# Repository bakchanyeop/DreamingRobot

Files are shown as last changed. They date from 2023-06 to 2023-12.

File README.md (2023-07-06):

# DreamingRobot

본 저작권은 꿈꾸는 로봇에 있습니다!

<br>
https://www.youtube.com/@Dreamingrobot<br>
▲ 꿈꾸는 로봇 Youtube 주소

안녕하세요! 꿈꾸는 로봇 꿈봇입니다.

본 깃허브는 제가 제작하는 과정의 코드와 STL 파일들을 올릴 예정입니다.

5개월간 짬짬이 만들은 로봇입니다.

현재 4족 로봇을 로보티즈 다이나믹셀 AX12로 제작중입니다.

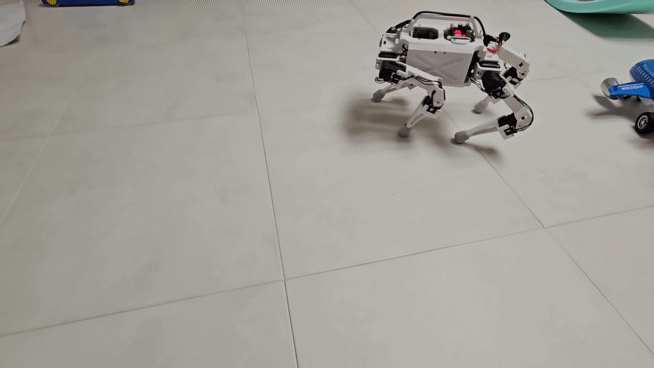
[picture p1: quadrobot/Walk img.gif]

▲ 보행 영상(이전 영상이라 지금 모델하고는 조금 차이가 있습니다)

# Model File

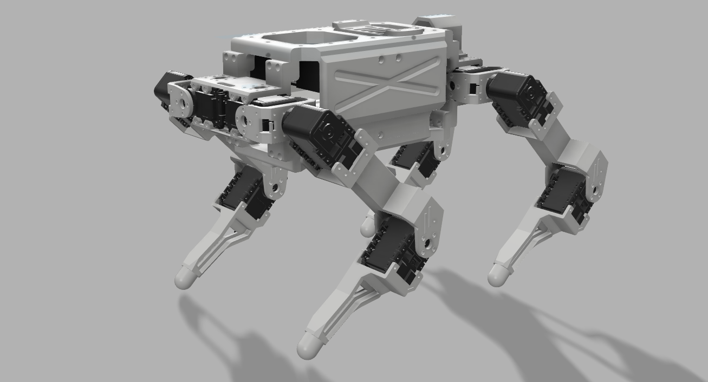
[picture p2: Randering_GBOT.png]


▲ 최종 조립 랜더링 이미지

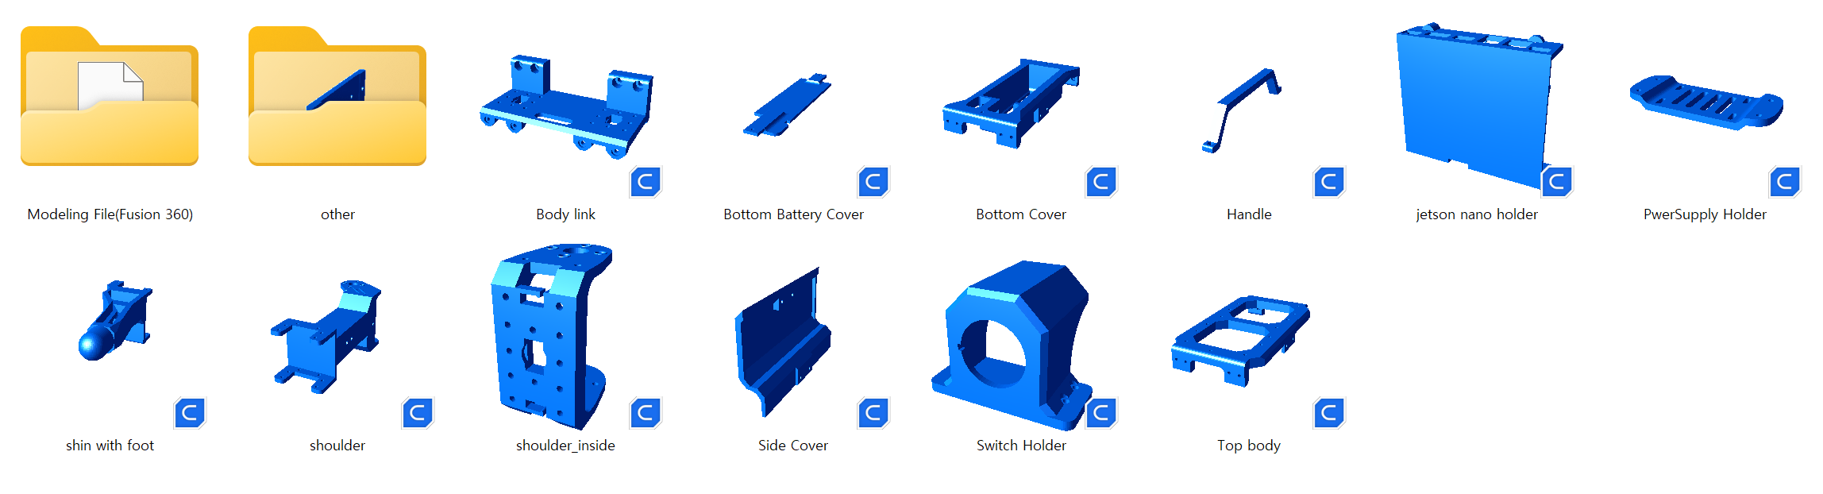
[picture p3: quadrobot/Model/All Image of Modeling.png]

' 모델 파일은 상단 이미지와 같으며 수량은 아래와 같습니다.

**Shoulder, Shin with foot은 큐라의 Mirror 기능으로 반대편 발도 출력 합니다.**

|순번|제목|수량|
|---|---|---|
|1|Body link|4EA|
|2|Bottom Battery Cover|1EA|
|3|Bottom Cover|1EA|
|4|Handle|1EA|
|5|jetson nano(ver.2GB Dev) holder|1EA|
|6|shoulder(right)|2EA|
|7|shoulder(left)|2EA|
|8|Shin with foot(right)|2EA|
|9|Shin with foot(left)|2EA|
|10|Sude Civer|2EA|
|11|Switch Holder|1EA|
|12|Top Body|1EA|
|13|shoulder_inside|1EA|

# 부속품

|순번|제목|수량|
|---|---|---|
|1|M2x8 Bolt Nut Set|52 EA|
|2|M2x6|48EA|
|3|M3x10 Bolt nut set|8Set|
|4|M3x10 Bolt|22EA|
|5|U2D2 변환기|1EA|
|6|젯슨나노2GB버전|1EA|
|7|XH-M609(리튬폴리머 방전 방지)|1EA|
|8|Switch|1EA|
|9|lithium Polymer 30C(11.1V)|1EA|
|10|Joystick|1EA|

# 조립 내용

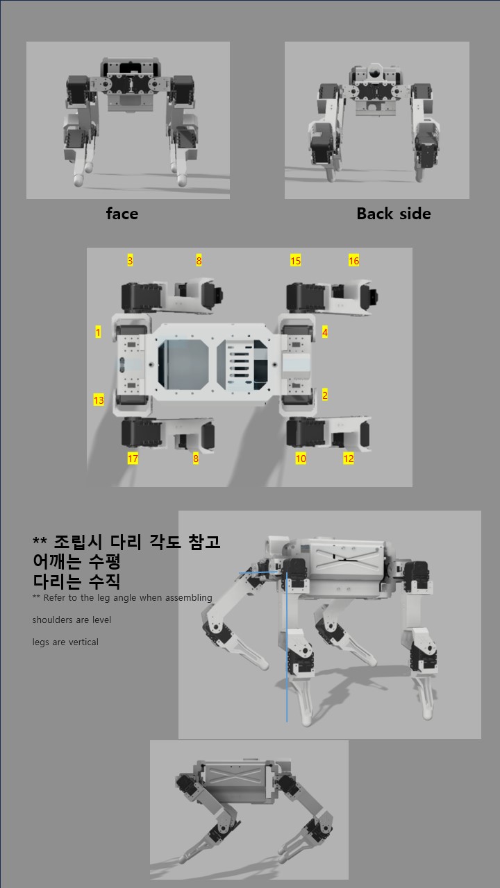
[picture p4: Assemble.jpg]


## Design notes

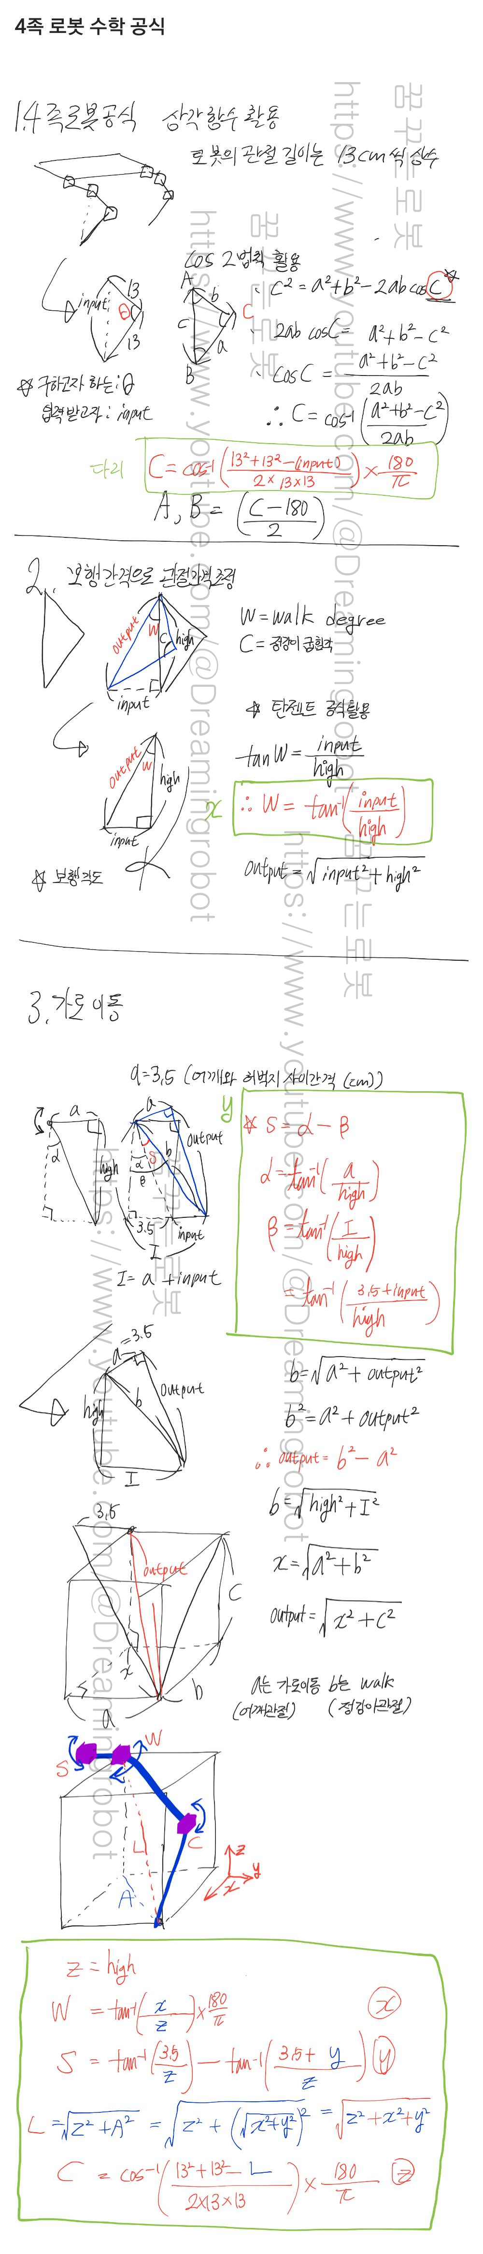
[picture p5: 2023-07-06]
quadrobot/Kinematics/Kinematics Img2.png

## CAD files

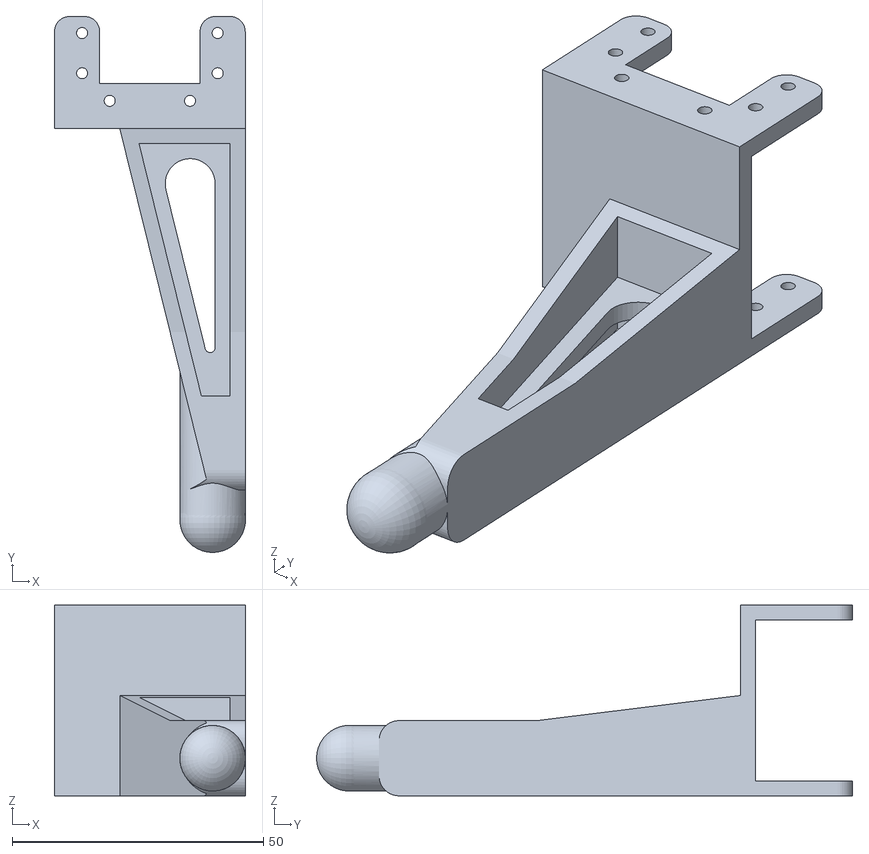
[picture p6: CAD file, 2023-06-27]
quadrobot/Model/other/NickM.STL
38.0 x 106.8 x 38.0

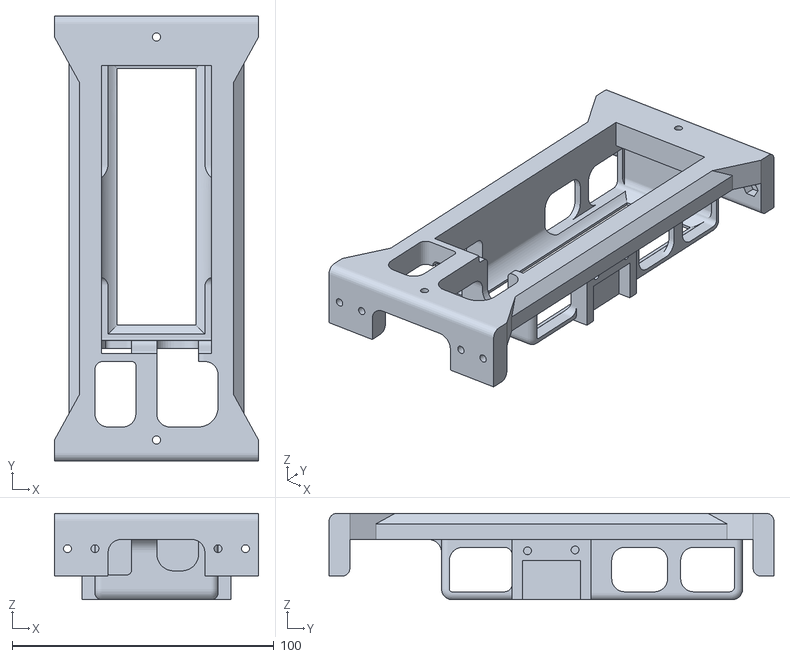
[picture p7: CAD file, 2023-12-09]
quadrobot/Model/몸통부 조립부2 v13.stl
78.0 x 170.0 x 33.0

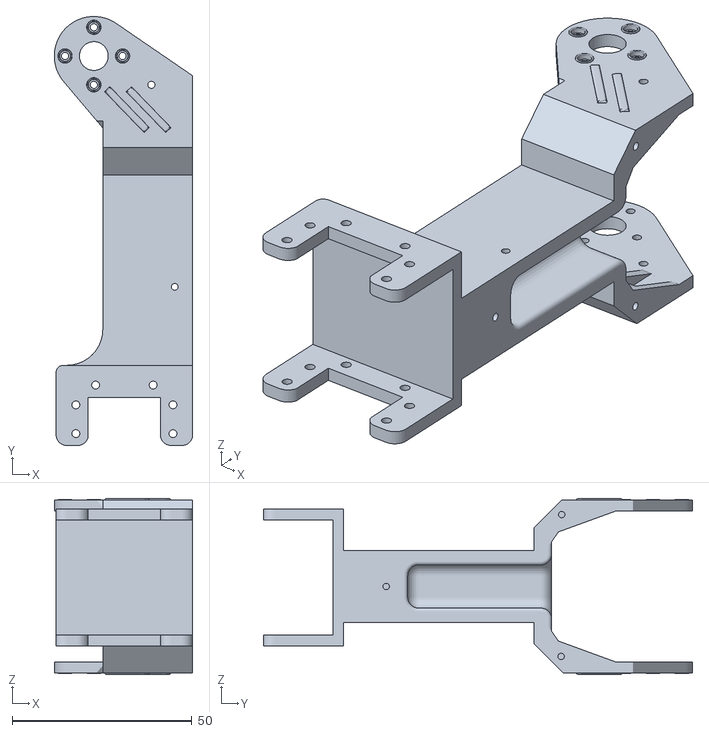
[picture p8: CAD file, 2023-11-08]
quadrobot/Model/Spring thighs.stl
38.5 x 119.3 x 49.0

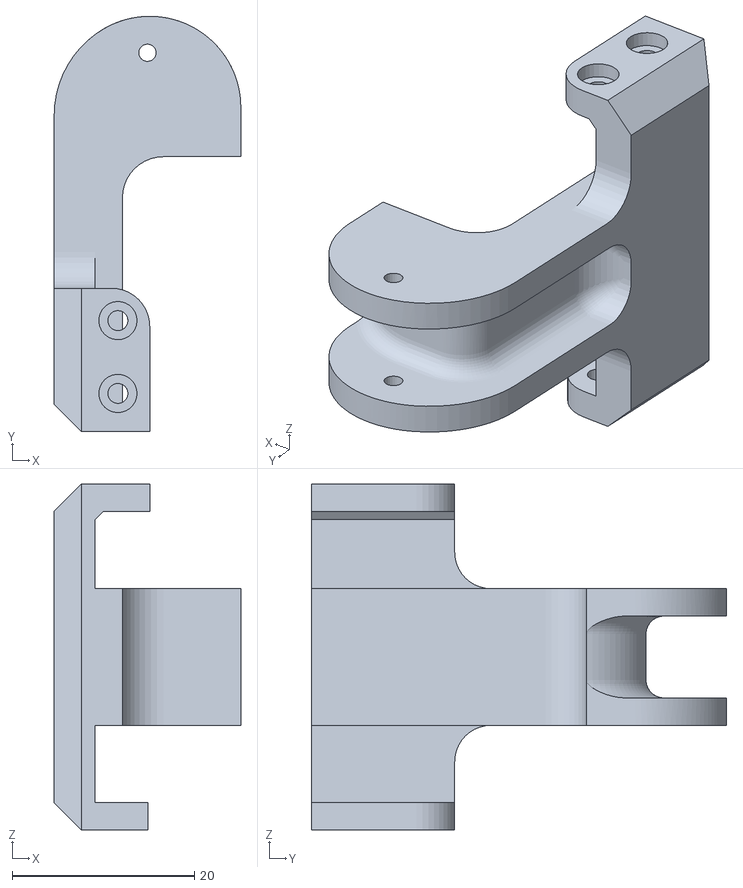
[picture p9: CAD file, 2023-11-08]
quadrobot/Model/AX-12 Spring.stl
20.5 x 45.6 x 38.0

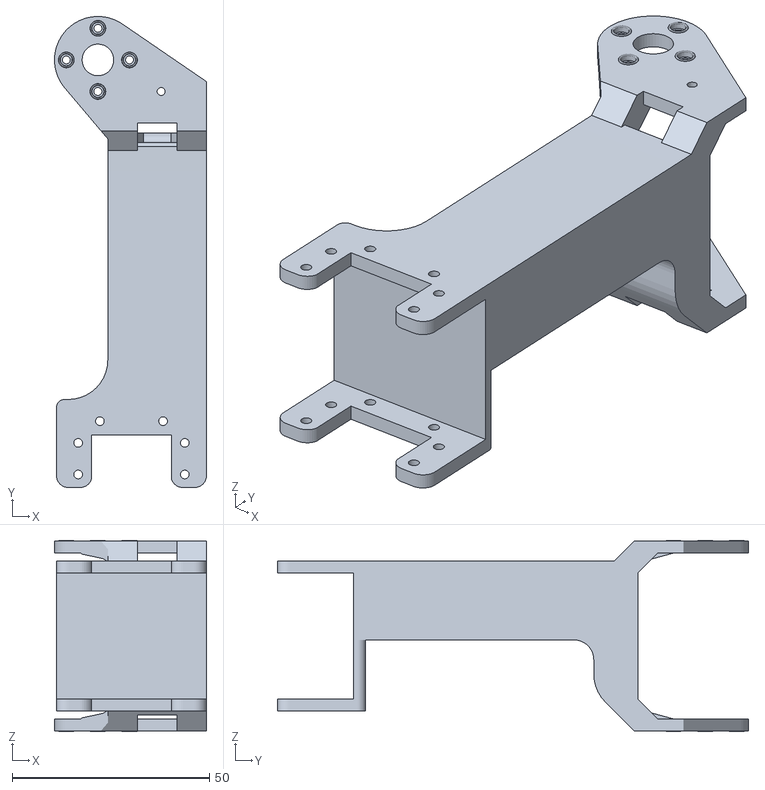
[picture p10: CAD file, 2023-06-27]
quadrobot/Model/other/hubug.STL
38.5 x 119.3 x 48.5

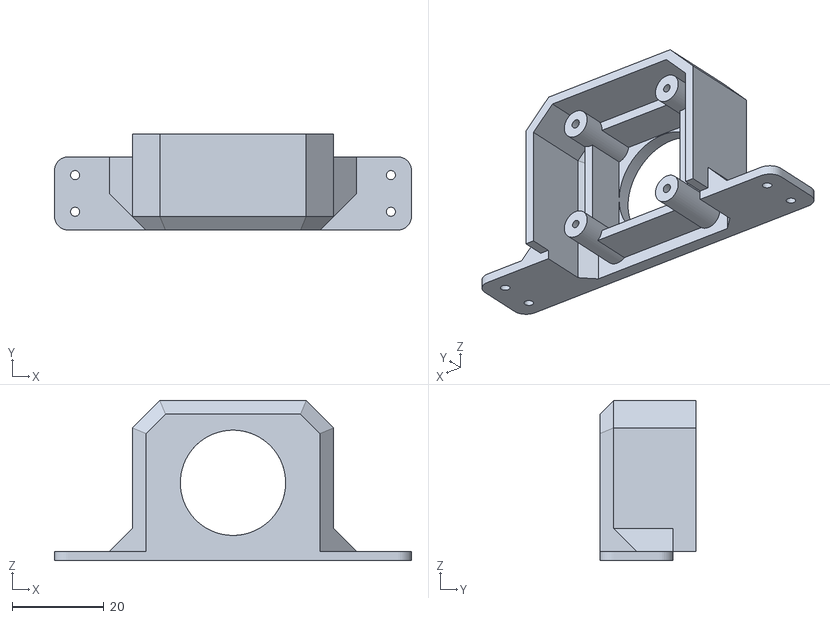
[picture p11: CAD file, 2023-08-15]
quadrobot/Model/CameraBase.stl
78.0 x 21.0 x 35.0

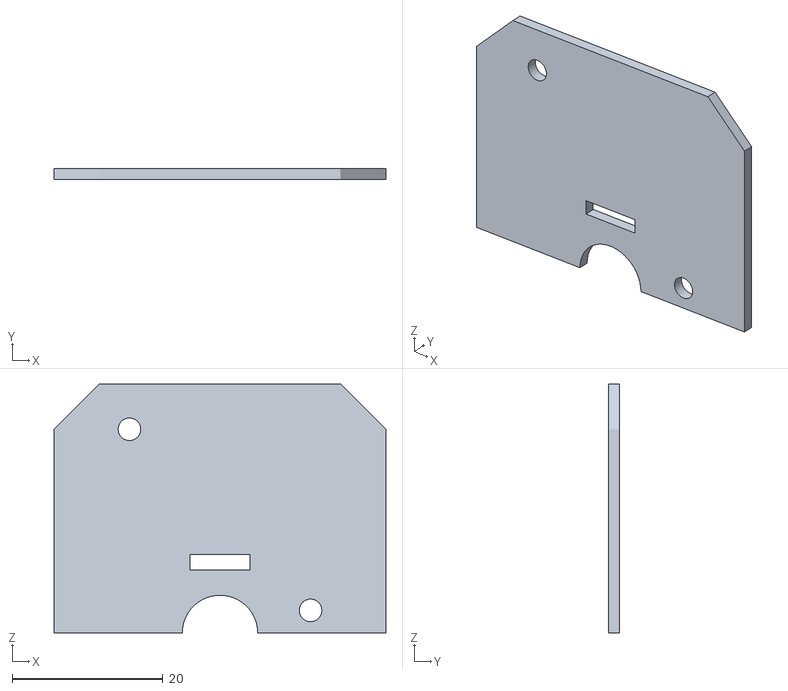
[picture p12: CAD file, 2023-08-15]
quadrobot/Model/CaneraCover.stl
44.0 x 1.50 x 33.0

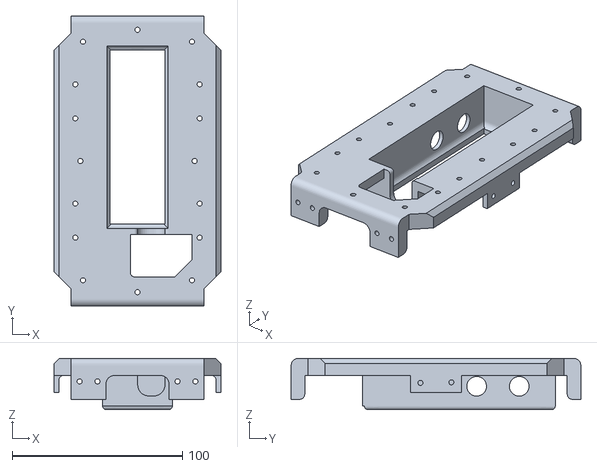
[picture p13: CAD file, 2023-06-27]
quadrobot/Model/other/몸통 배터리부 v10.stl
98.0 x 170.0 x 30.0

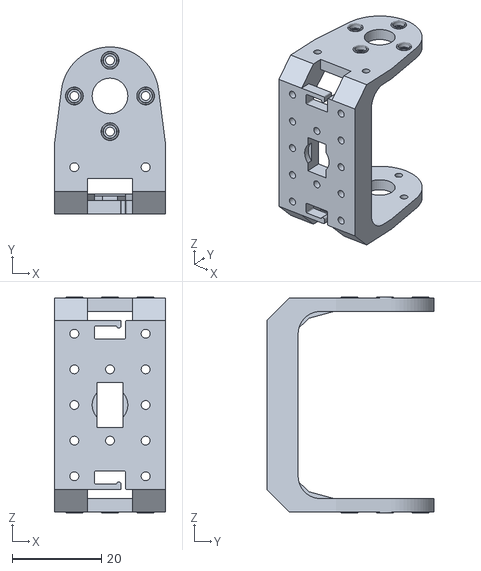
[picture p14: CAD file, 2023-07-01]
quadrobot/Model/shoulder_inside.stl
25.0 x 37.5 x 48.5

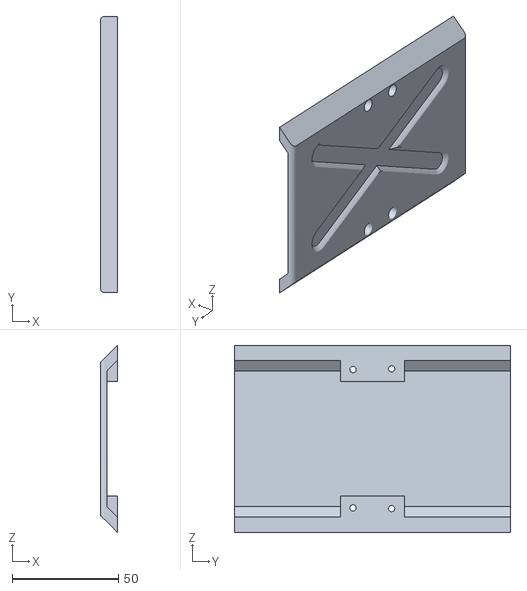
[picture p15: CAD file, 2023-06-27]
quadrobot/Model/other/side Cover.stl
8.00 x 130.0 x 88.0

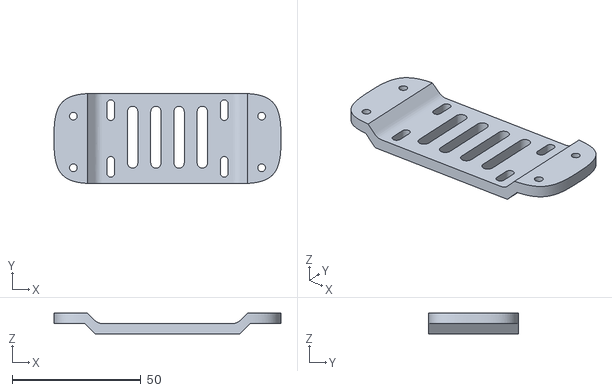
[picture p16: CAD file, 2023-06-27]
quadrobot/Model/PwerSupply Holder.stl
88.0 x 35.0 x 8.00

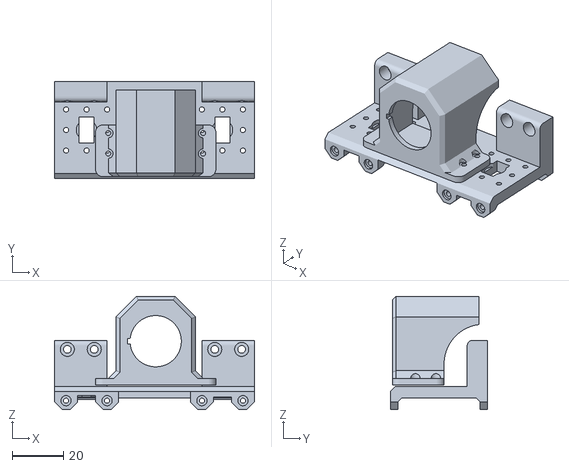
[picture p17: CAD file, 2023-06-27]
quadrobot/Model/other/스위칭 고정부.stl
78.0 x 38.0 x 44.2

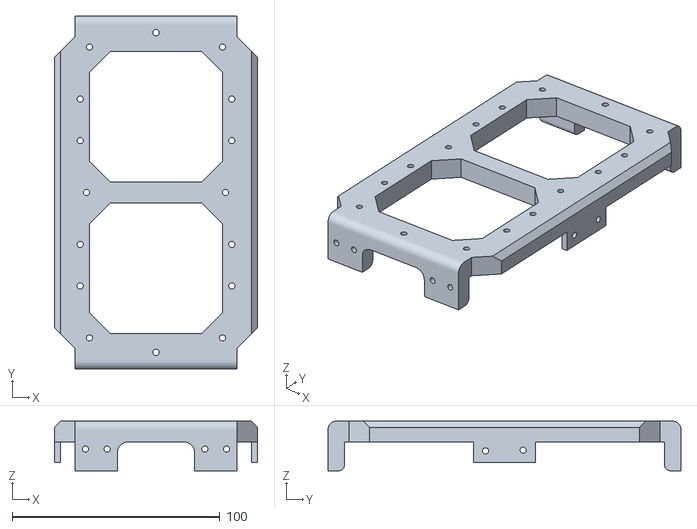
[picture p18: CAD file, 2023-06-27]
quadrobot/Model/Top body.stl
98.0 x 170.0 x 24.0

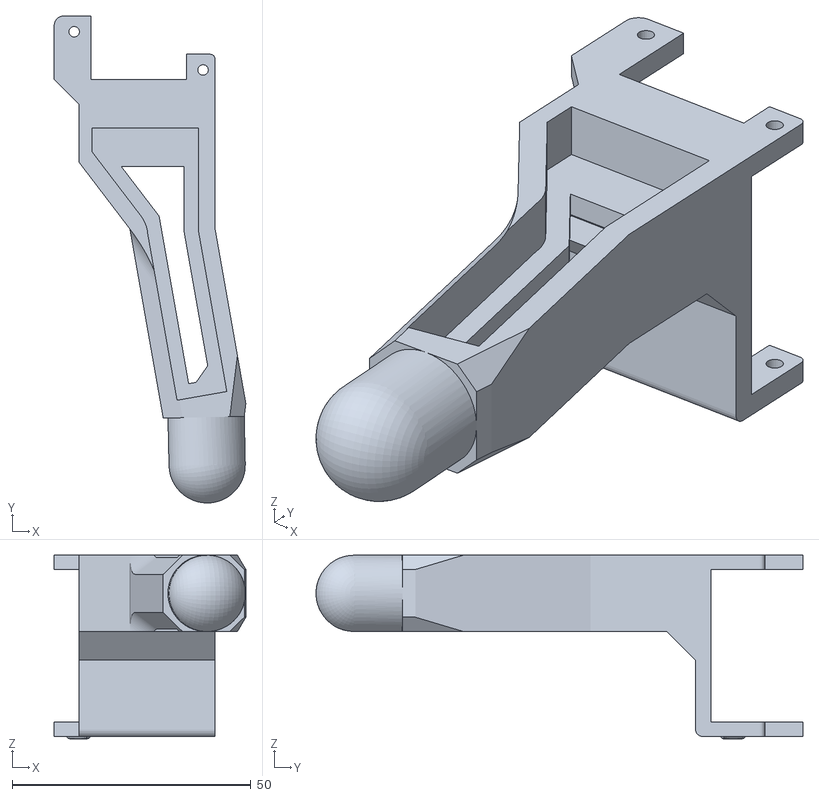
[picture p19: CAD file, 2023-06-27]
quadrobot/Model/shin with foot.stl
40.2 x 102.0 x 38.5

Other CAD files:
quadrobot/Model/other/몸통부 조립부2 v12.stl
quadrobot/Model/other/Nick.STL
quadrobot/Model/other/hubugM.STL
quadrobot/Model/other/배터리 커버.stl
quadrobot/Model/Body link.stl
quadrobot/Model/Bottom Battery Cover.stl
quadrobot/Model/Bottom Cover.stl
quadrobot/Model/Handle.stl
quadrobot/Model/Modeling File(Fusion 360)/Bottom Body with Battery Cover.f3d
quadrobot/Model/Modeling File(Fusion 360)/Bottom Body.f3d
quadrobot/Model/Modeling File(Fusion 360)/PowerSupply Holder.f3z
quadrobot/Model/Modeling File(Fusion 360)/Switch Holder.f3d
quadrobot/Model/Modeling File(Fusion 360)/Top Body.f3d
quadrobot/Model/Modeling File(Fusion 360)/leg.f3d
quadrobot/Model/Modeling File(Fusion 360)/shoulder.f3d
quadrobot/Model/Side Cover.stl
quadrobot/Model/Switch Holder.stl
quadrobot/Model/jetson nano holder.stl
quadrobot/Model/other/몸통 배터리부 v1.f3d
quadrobot/Model/other/몸통 배터리부 v9.stl
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

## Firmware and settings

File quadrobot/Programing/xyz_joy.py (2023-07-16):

##################################################
##    꿈꾸는 로봇 Quadruped Robot Program          #
##  https://www.youtube.com/@Dreamingrobot       #
## https://github.com/bakchanyeop/DreamingRobot/ #
##################################################
## 저작권은 꿈꾸는 로봇 에 있습니다                                                         #
## Copyright(C) 2023. DreamingRobot-BAKCHANYEOP. All rights reserved.#


from dynamixel_sdk import *
import time
import math
import pygame
import threading


a_leg=13
b_leg=13
shder=3.5 #sholder cm(new)


    
def CTD(data):
    degrees=round((data/300)*1023)
    return degrees


# 사용할 포트와 프로토콜 버전 설정
PORT = '/dev/ttyUSB0'
BAUDRATE = 1000000
PROTOCOL_VERSION = 1.0




# 모터 ID와 모터의 최대, 최소 각도 설정
ID = [13, 17, 18, 10, 12, 2]
MIN_ANGLE = 0
MAX_ANGLE = 1023



index=0
# 포트 열기
portHandler = PortHandler(PORT)
portHandler.openPort()

# 포트 설정
packetHandler = PacketHandler(PROTOCOL_VERSION)
#packetHandler.setBaudRate(BAUDRATE)

portHandler.setBaudRate(BAUDRATE)



def on_key(event):
    print('Key Pressed:', event.name)

# 모터 초기 설정
for id in ID:

    dxl_comm_result, dxl_error = packetHandler.write1ByteTxRx(portHandler, id, 24, 1) # 모터 회전 가능하도록 설정
    dxl_comm_result, dxl_error = packetHandler.write2ByteTxRx(portHandler, id, 32, 22) # 모터 최소 speed
    dxl_comm_result, dxl_error = packetHandler.write2ByteTxRx(portHandler, id, 6, MIN_ANGLE) # 모터 최소 각도 설정
    dxl_comm_result, dxl_error = packetHandler.write2ByteTxRx(portHandler, id, 8, MAX_ANGLE) # 모터 최대 각도 설정
    print('seeeeeeeet')

# groupSyncWrite 객체 생성
groupSyncWrite = GroupSyncWrite(portHandler, packetHandler, 30, 4)

Center_Data=CTD(150)


################

# 초기화
pygame.init()
pygame.joystick.init()



# 조이스틱 개수 확인
joystick_count = pygame.joystick.get_count()
if joystick_count == 0:
    print("No joystick detected.")
    exit()

# 첫 번째 조이스틱 가져오기
joystick = pygame.joystick.Joystick(0)
joystick.init()

# 인터럽트 함수
def perform_interrupt(direction):
    print("Interrupt occurred! Direction: {}".format(direction))
    # 여기에 인터럽트 동작을 수행하는 코드를 추가하세요

# 이벤트 처리 스레드



def event_thread():
    
    global my_walk 
    global my_walk_1
    global delay ##초기 상태
    while True:
        for event in pygame.event.get():
            if event.type == pygame.JOYAXISMOTION:  # 조이스틱 축 움직임 이벤트
                axis = event.axis
                value = event.value

                if axis == 0:  # X 축 (좌우)
                    if value < -0.5:
                        perform_interrupt("Left")
                        my_walk = [(0, 5, 15),(0, 4, 18),(0, 2, 18),(0, 0, 18),(0, 5, 15),(0, 4, 18)]
                        my_walk_1 =[(0, -5, 15),(0, -4, 18),(0, -2, 18), (0, 0, 18),(0, -5, 15),(0, -4, 18)]
                        delay=0.03
                    elif value > 0.5:
                        perform_interrupt("Right")
                        my_walk_1= [(0, 5, 15),(0, 4, 18),(0, 2, 18),(0, 0, 18),(0, 5, 15),(0, 4, 18)]
                        my_walk =[(0, -5, 15),(0, -4, 18),(0, -2, 18), (0, 0, 18),(0, -5, 15),(0, -4, 18)]
                        delay=0.03
                elif axis == 1:  # Y 축 (전후)
                    if value < -0.5:
                        perform_interrupt("Forward")        
                        my_walk = [(2,0,18),(-2,0,18),(-6,0,18), (3,0,15),(2,0,18),(-2,0,18)]
                        my_walk_1 = [(2,0,18),(-2,0,18),(-6,0,18), (3,0,15),(2,0,18),(-2,0,18)]
                        delay=0.01
                    elif value > 0.5:
                        perform_interrupt("Backward")
                        my_walk = [(2,0,18),(-3,0,15),(-3,0,18), (-1,0,18),(2,0,18),(-3,0,15)]
                        my_walk_1 =  [(2,0,18),(-3,0,15),(-3,0,18), (-1,0,18),(2,0,18),(-3,0,15)]
                        delay=0.01
                else:
                    print("stop")
                    my_walk = [(0,0,18),(0,0,18),(0,0,18), (0,0,18),(0,0,18),(0,0,18)]
                    my_walk_1 = [(0,0,18),(0,0,18),(0,0,18), (0,0,18),(0,0,18),(0,0,18)]
            elif event.type == pygame.JOYBUTTONDOWN:  # 조이스틱 버튼 누름 이벤트
                button = event.button
                print("Button {} pressed".format(button))
                # 여기에 버튼 누름 이벤트를 처리하는 코드를 추가하세요
                if button == 1:
                    print("stop")
                    my_walk = [(0,0,18),(0,0,18),(0,0,18), (0,0,18),(0,0,18),(0,0,18)]
                    my_walk_1 = [(0,0,18),(0,0,18),(0,0,18), (0,0,18),(0,0,18),(0,0,18)]##초기 상태
            
            elif event.type == pygame.JOYBUTTONUP:  # 조이스틱 버튼 떼기 이벤트
                button = event.button
                print("Button {} released".format(button))
                my_walk = [(0,0,18),(0,0,18),(0,0,18), (0,0,18),(0,0,18),(0,0,18)]
                my_walk_1 = [(0,0,18),(0,0,18),(0,0,18), (0,0,18),(0,0,18),(0,0,18)]
                # 여기에 버튼 떼기 이벤트를 처리하는 코드를 추가하세요
my_walk = [(0,0,18),(0,0,18),(0,0,18), (0,0,18),(0,0,18),(0,0,18)]
my_walk_1 = [(0,0,18),(0,0,18),(0,0,18), (0,0,18),(0,0,18),(0,0,18)]
delay=0.01
# 이벤트 처리 스레드 시작
event_thread = threading.Thread(target=event_thread)
event_thread.daemon = True
event_thread.start()




# 메인 루프
while (1):
    


     
    count=4    
    for count in range(0,count):
    
##################


        x, y, z = my_walk[count]        
      
        W=math.atan(x/z)*180/3.14
        S=(math.atan(3.5/z)-math.atan((3.5+y)/z))*180/3.14
        A=math.sqrt(x**2+y**2)
        L=math.sqrt(z**2+A**2)
        C=math.acos((13**2+13**2-L**2)/(2*13*13))*180/3.14



        S_out=S        	
        C_Degree=C
        walk_deg=W      
##################        
     
        
        print('OutPut')

    

        
        x, y, z = my_walk_1[count+2]        
      
        W=math.atan(x/z)*180/3.14
        S=(math.atan(3.5/z)-math.atan((3.5+y)/z))*180/3.14
        A=math.sqrt(x**2+y**2)
        L=math.sqrt(z**2+A**2)
        C=math.acos((13**2+13**2-L**2)/(2*13*13))*180/3.14

        
        S_out_1=S        
        C_Degree_1=C
        walk_deg_1=W        

        w_offset=4
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

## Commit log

2023-06-27 Create STL Program
2023-06-27 STL 파일 정리 및 Upload
    STL 파일 정리 및 Upload
    [Body link.stl, Bottom Battery Cover.stl, Bottom Body with Battery Cover.f3d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]
2023-06-28 Update Readme 파일
    리스트 업데이트
2023-06-29 Update README.md
    업데이트
2023-06-29 Add files via upload
    워킹 gif파일
2023-06-29 Create kinematics
2023-07-01 Add files via upload
    겨드랑이부
    [shoulder_inside.stl]
2023-07-01 Add files via upload
    shoulder inside 추가
2023-07-02 Add files via upload
    조립 방법 등록
